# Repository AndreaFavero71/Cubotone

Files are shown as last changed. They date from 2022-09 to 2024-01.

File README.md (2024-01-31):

# CUBOTone

This repo contains the files to build CUBOTone, my first Rubik’s cube solver robot.<br />
CUBOTone uses servos and stepper motor resulting in a faster solving time than the newer CUBOTino series.

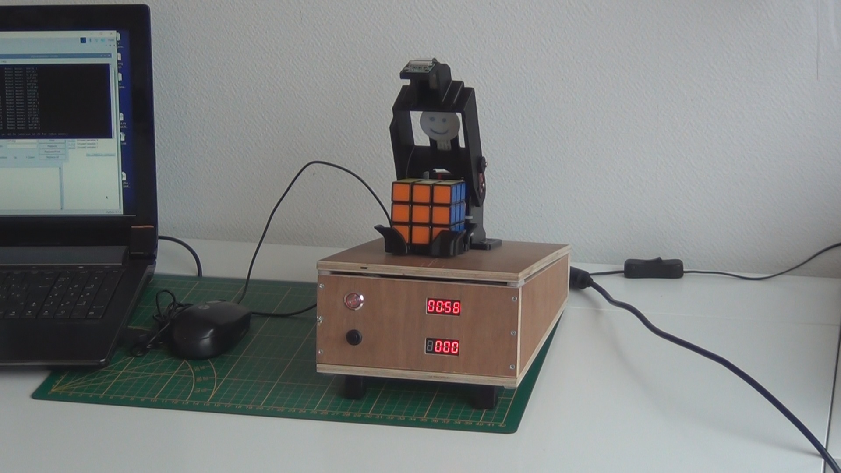
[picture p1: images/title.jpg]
title image


Further robot info at: https://www.instructables.com/Rubik-Cube-Solver-Robot-With-Raspberry-Pi-and-Pica/

An impression of the robot: https://www.youtube.com/watch?v=oYRXe4NyJqs

This git repo simplifies the download of the individual files and automates as much a possible the deployment to the Raspberry Pi

# How to use it:
1. Flash your SD card according to the procedure in the [document here](doc/How_to_make_CUBOTone_robot_20240131.pdf) , Chapter 8
2. Put the sd card in the pi and power it. You can monitor the boot process if you connect an hdmi monitor to it but it is not essential. 
3. Try to connect to the Raspberry Pi via SSH. On Windows you can use Putty. On linux and mac you can type directly:
```
ssh pi@cubotone.local
```
4. If you can’t reach the pi like this, you will have to scan your network to find the IP to use
5. After you are connected via ssh, type the following commands in the shell:
```
git clone https://github.com/AndreaFavero71/cubotone.git
cd cubotone/src
sudo ./install/setup.sh
```
6. Make sure the script runs without error until the end. It should ask you to reboot. Type ‘y’ and hit enter. You should get the proper environment after reboot at that point
7. If there is any error during the script execution try to fix it and rerun the script again

# Executing manually
From a shell, you can run the main python script like this:
```
cd ~/cubotone/src
source .virtualenvs/bin/activate
python Cubotone.py
```
of course, you can replace `Cubotone.py` by any other python scripts as mentioned in the documentation.

# Enabling autostart
When everything is tuned and you want to autostart the software automatically on reboot, just type :
```
    sudo crontab -e
```
select the nano editor ‘1’ then go to the last line of the window and remove the first ‘#’ character of the line . This uncomment the startup script that launches cubotino on startup. You can reboot after to test it.

# VNC connection
You can always connect with ssh. If you prefere VNC you can download the RealVNC client (this is the one I use). You just have that start it like this:
```
vncviewer cubotone.local
```
It will ask for the credential. Use ‘pi’ and the same password you use for ssh. You should have a desktop version in this way

Check out the "How_to_make ...  .pdf" document (at /doc folder) for further info

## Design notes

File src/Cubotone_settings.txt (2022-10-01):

{
"camera_width_res": "800",
"camera_hight_res": "544",
"zoom_x":0.0,
"zoom_y":0.0,
"zoom_w":1,
"zoom_h":1,
"kl": "0.95",
"scale_perc": "65",
"square_ratio": "2",
"rhombus_ratio": "0",
"delta_area_limit": "0.7",
"sv_max_moves": "20",
"sv_max_time": "2",
"collage_w": "1024",
"marg_coef": "0.1",
"cam_led_bright": "300",
"detect_timeout": "40",
"show_time": "7",
"gap_w": "60",
"gap_h": "100"
}

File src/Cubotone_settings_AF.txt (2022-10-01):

{
"camera_width_res": "800",
"camera_hight_res": "544",
"zoom_x":0.0,
"zoom_y":0.0,
"zoom_w":0.75,
"zoom_h":0.82,
"kl": "0.95",
"scale_perc": "65",
"square_ratio": "2",
"rhombus_ratio": "0",
"delta_area_limit": "0.7",
"sv_max_moves": "20",
"sv_max_time": "2",
"collage_w": "1024",
"marg_coef": "0.1",
"cam_led_bright": "300",
"detect_timeout": "40",
"show_time": "7",
"gap_w": "60",
"gap_h": "100"
}

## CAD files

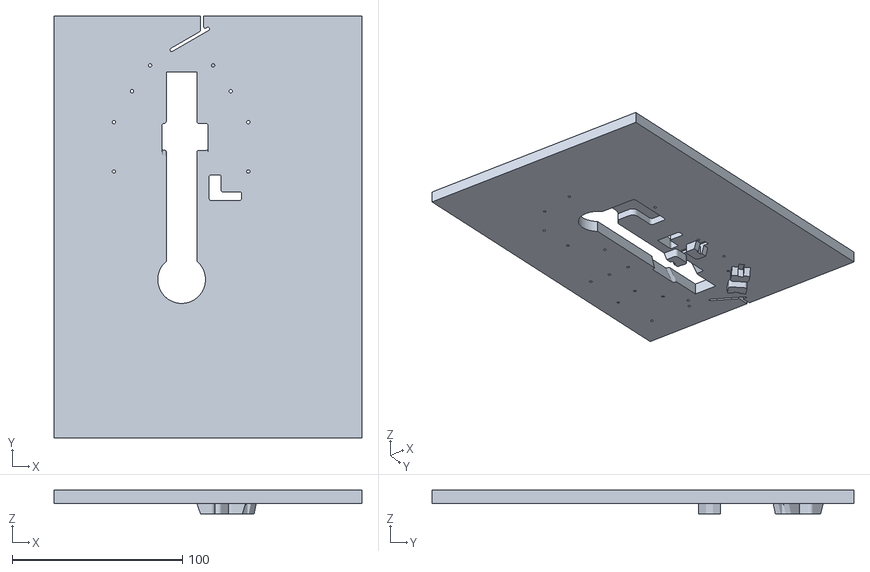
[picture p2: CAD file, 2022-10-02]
stl/Panel_top.stl
181.0 x 248.0 x 14.0

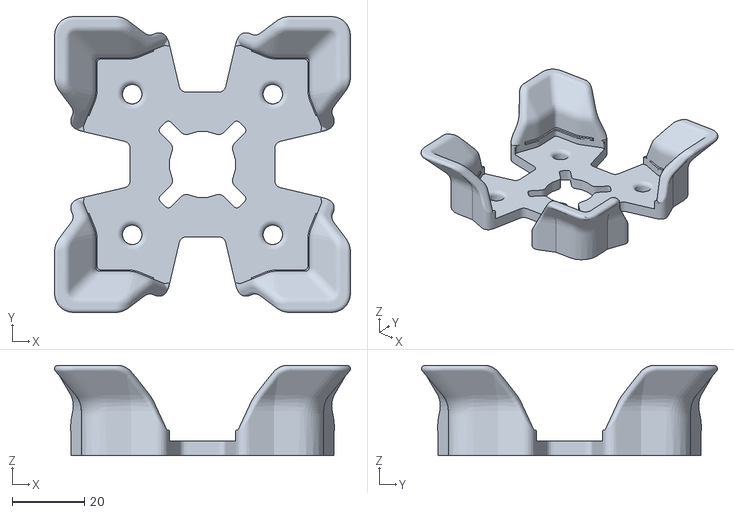
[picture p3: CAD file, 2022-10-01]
stl/Cube_holder_upper_part.stl
81.9 x 81.9 x 25.0

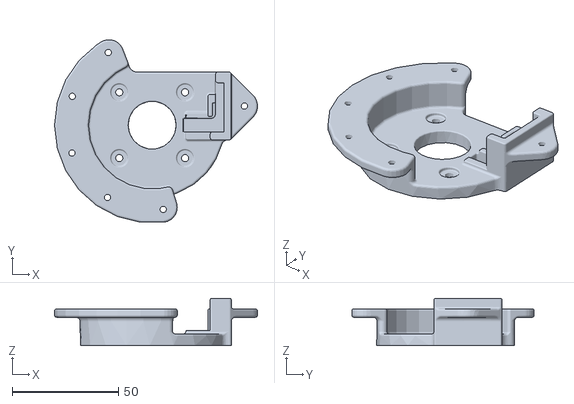
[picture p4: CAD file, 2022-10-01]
stl/Motor_support.stl
95.6 x 85.9 x 22.1

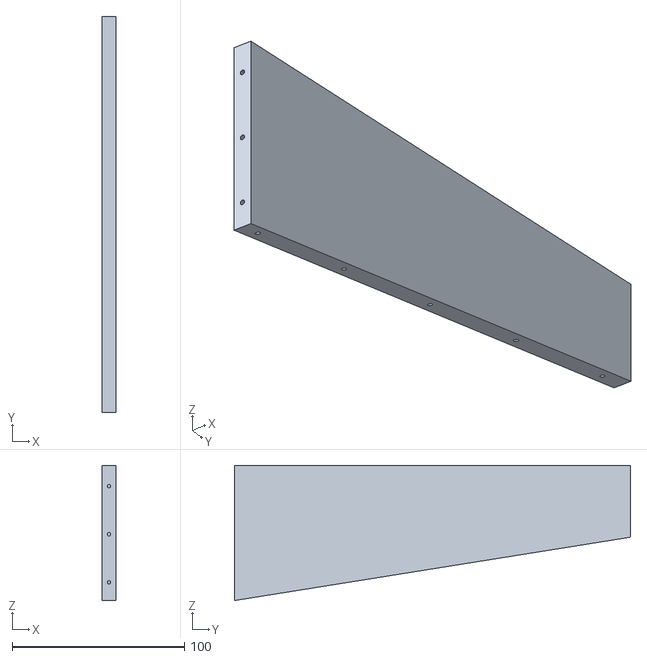
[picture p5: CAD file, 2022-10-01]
stl/Panel_left.stl
8.00 x 230.0 x 78.5

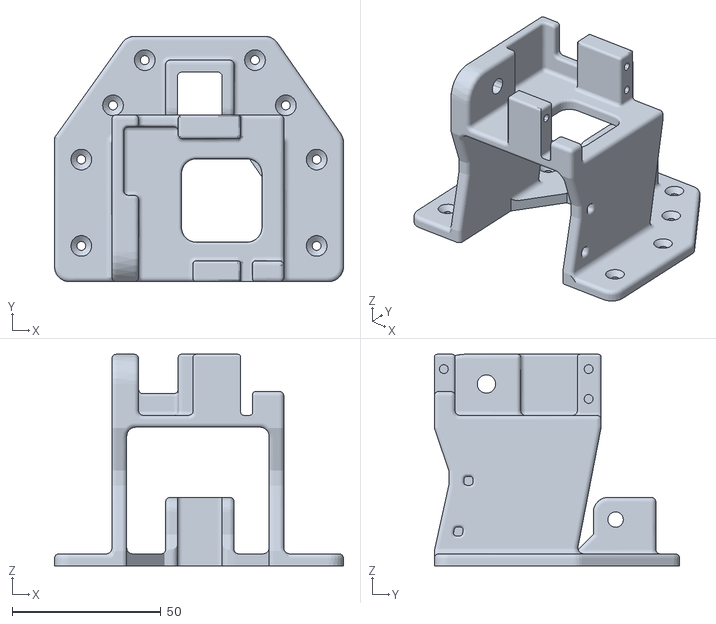
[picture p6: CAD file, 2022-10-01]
stl/Hinge_upperCover_Lifter.stl
97.0 x 82.4 x 71.0

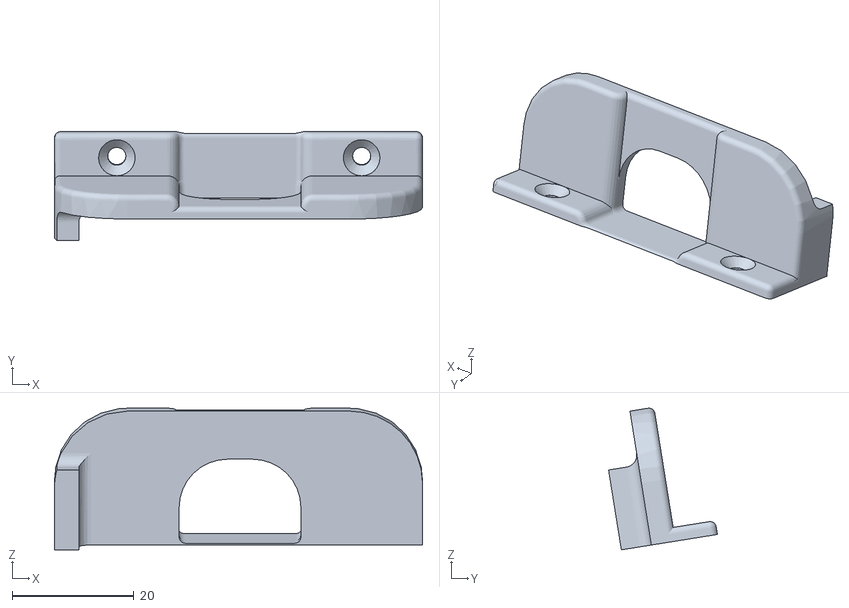
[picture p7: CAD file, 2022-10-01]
stl/Rpi_holder_back.stl
60.5 x 17.9 x 23.3

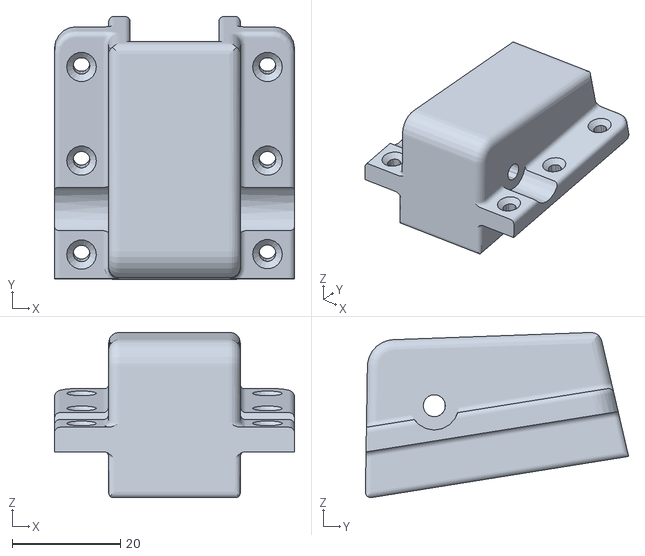
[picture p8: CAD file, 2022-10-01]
stl/Foot_hinge.stl
44.4 x 48.7 x 30.5

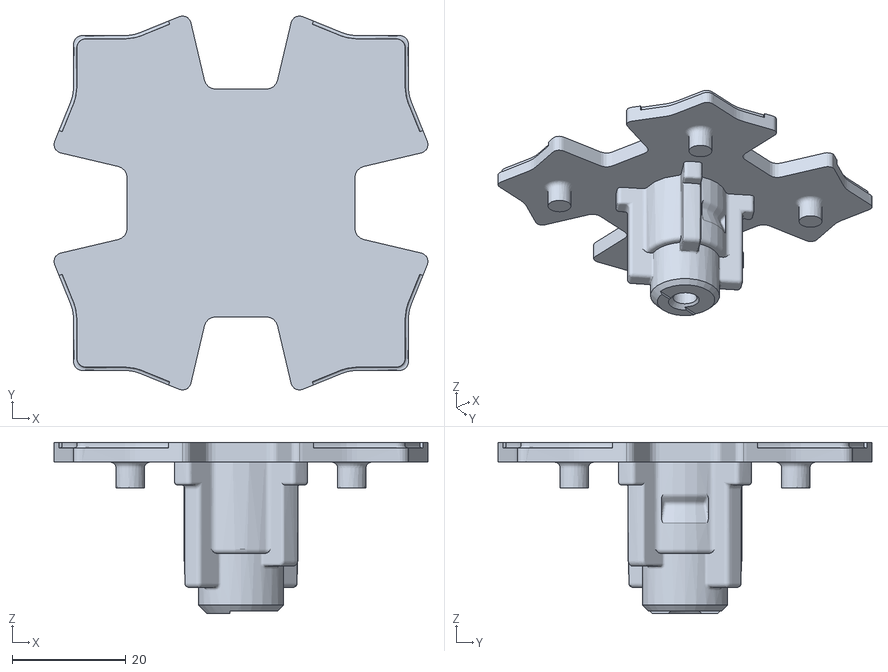
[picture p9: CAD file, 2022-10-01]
stl/Cube_holder_lower_part.stl
65.7 x 65.7 x 30.1

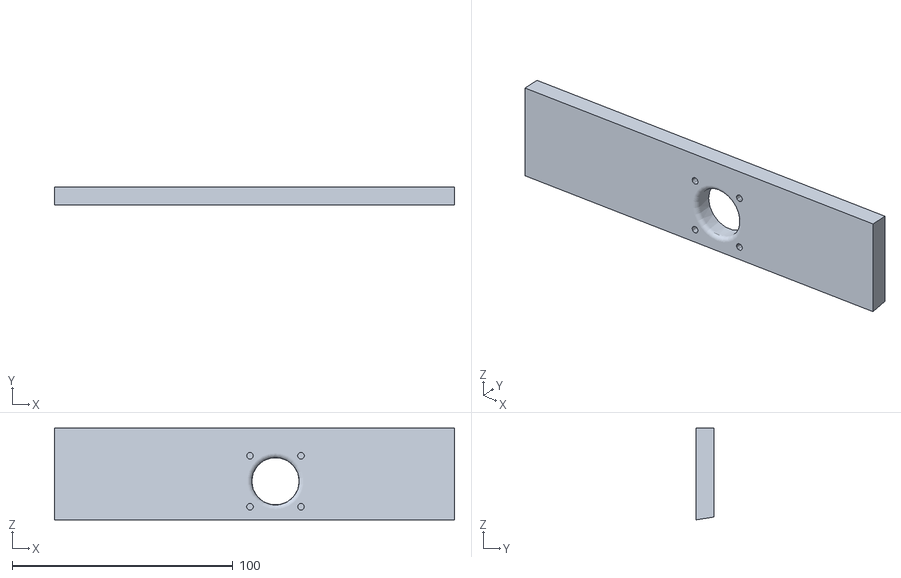
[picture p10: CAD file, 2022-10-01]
stl/Panel_back.stl
181.0 x 8.00 x 41.5

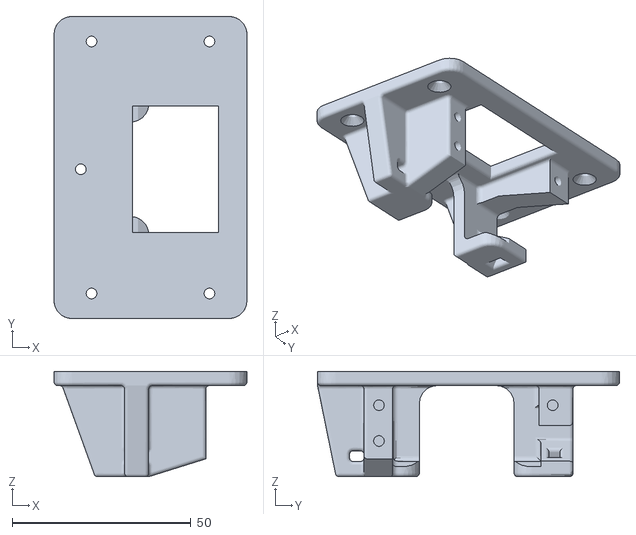
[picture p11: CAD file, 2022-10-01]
stl/Lifter_servo_holder.stl
54.0 x 84.5 x 29.5

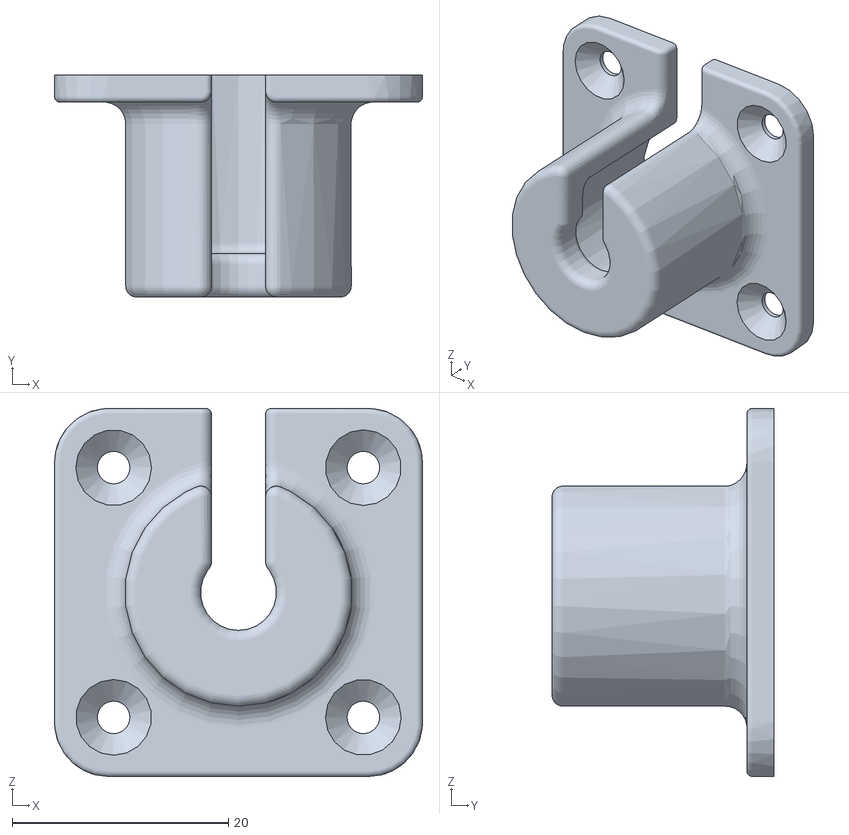
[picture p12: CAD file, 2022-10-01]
stl/Power_connector_inner_part.stl
34.0 x 20.5 x 34.0

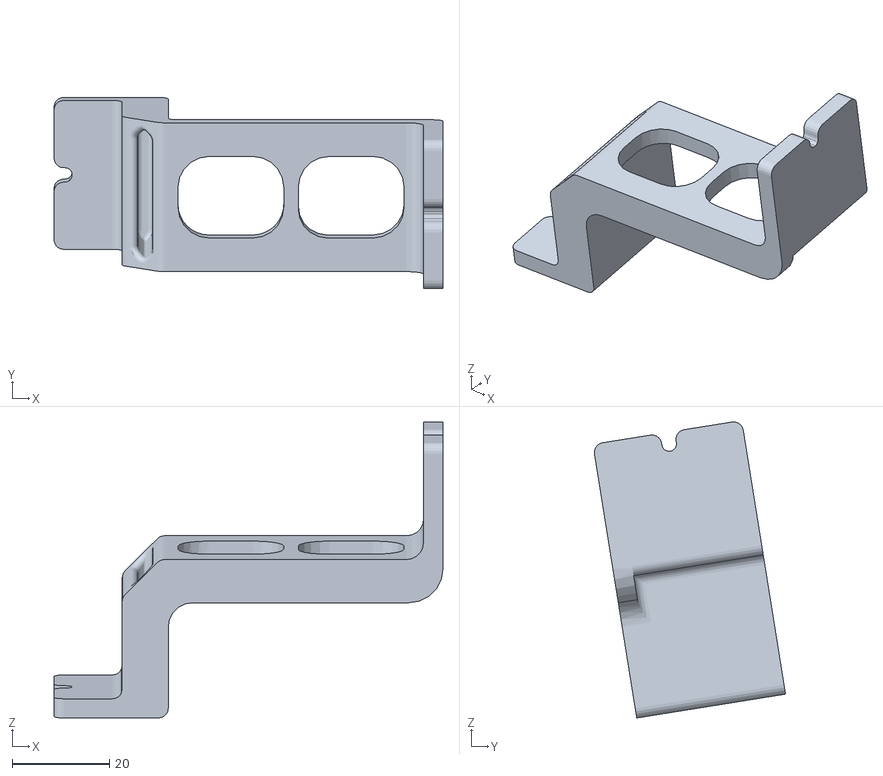
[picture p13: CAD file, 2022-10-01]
stl/Rpi_holder_front.stl
80.0 x 39.3 x 60.9

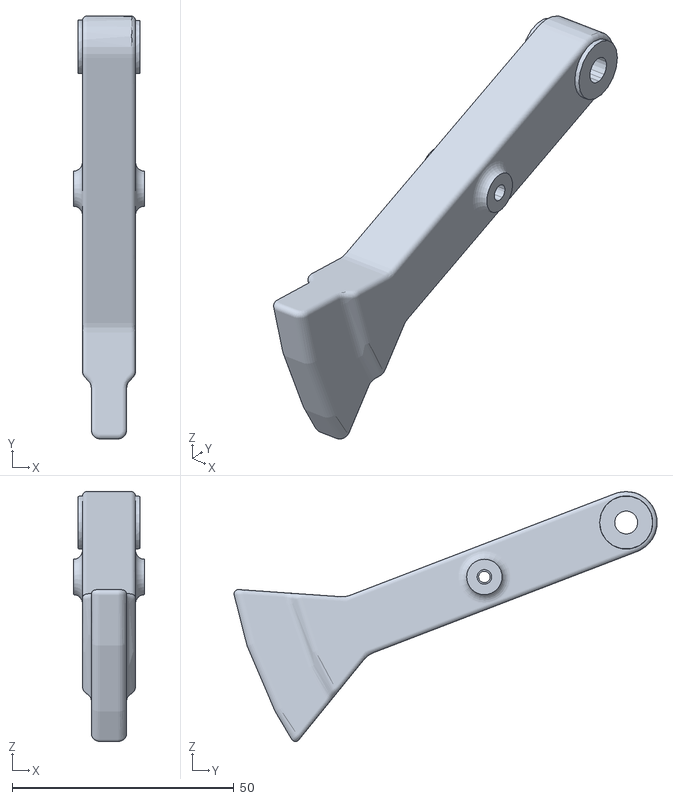
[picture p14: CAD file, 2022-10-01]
stl/Lifter.stl
16.0 x 95.5 x 56.4

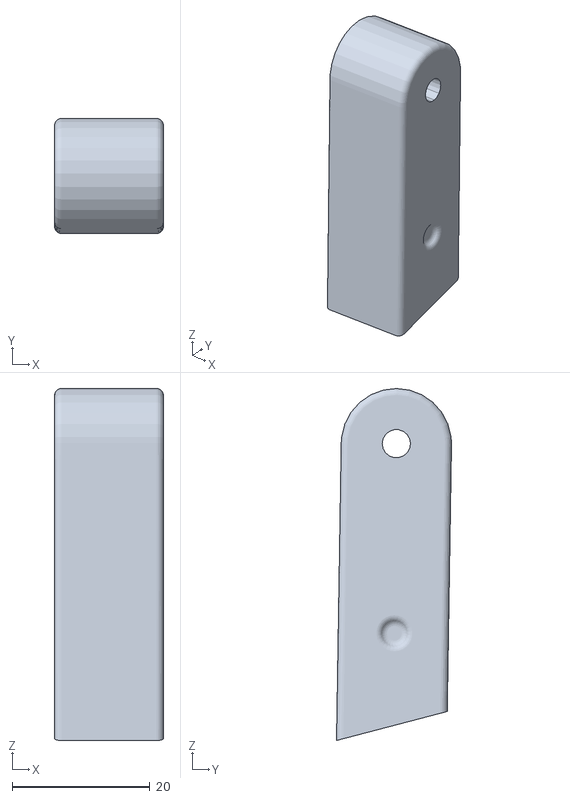
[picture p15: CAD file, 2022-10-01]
stl/Foot.stl
15.8 x 16.7 x 51.0

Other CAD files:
stl/PiCamera_holder.stl
stl/Power_connector_outer_part.stl
stl/Lever_link.stl
stl/Panel_bottom.stl
stl/Motor_sync_disk.stl
stl/Panel_front.stl
stl/Panel_right.stl

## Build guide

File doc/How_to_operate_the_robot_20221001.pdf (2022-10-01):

How to operate the robot: | 01 October 2022

Robot instructions (How_to_operate_the_robot_20221001.docx or .pdf):

SHUTDOWN: Closes the Raspberry Pi OS, wait 15 seconds before to unplug the robot.
BOOT: After a shutdown, a short press starts the boot (takes 30secs to complete); Boot starts automatically after the robot is plugged.
START: Only when Display2 shows Press.
STOP: Stops the robot, at any moment, when it is “moving”; If the button is released within 5 seconds the python script is reloaded and the robot gets ready again for a new cycle.
RESET: Ends the python script. Raspberry Pi OS remains up (use SHUTDOWN before unplug).

The robot has 2 main working modes:
A) Without any screen connected; This is the default mode, that starts once the robot is energized.
B) With a screen connected, by wiring or via SSH.

To quit mode A) or B), press STOP for 5 seconds. Displays segments go full ON and OFF shortly after.

To start mode B):
- Quit mode A)
- Connect to the raspberry pi (i.e. with VNC viewer, via SSH)
- Activate the virtual environment (source /home/pi/.virtualenvs/bin/activate)
- From root (/home/pi) enter the cube folder (cd cubotone/src)
- Run the python script (python Cubotone.py)
- SHUTDOWN (led goes OFF)
- BOOT (led goes ON in 30 secs)
- LOADING STATUS
- TIMER
- START
- STOP (0.5s < press < 5 sec)
- RESET (>5 sec press)
- INFO
- COUNTDOWN MOVES

## Display 1

## Display 2

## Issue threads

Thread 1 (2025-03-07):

Installation Issues: opencv-contrib-python==4.1.0.25 Not Found & CMake Build Fails with pytoml.core.TomlError

chiptrap, 2025-03-07:
Hello,

I'm experiencing two separate issues while attempting to install our OpenCV dependency for the Cubotone project on my Raspberry Pi 4. Below are the two error messages I’m encountering:

Error 1: Version Not Found

When I try to install:

`pip install opencv-contrib-python==4.1.0.25`
I receive the following error:

```
Could not find a version that satisfies the requirement opencv-contrib-python==4.1.0.25 (from versions: 3.4.11.45, 3.4.13.47, 3.4.14.51, 3.4.15.55, 3.4.16.59, 3.4.17.61, 3.4.17.63, 3.4.18.65, 4.4.0.46, 4.5.1.48, 4.5.2.52, 4.5.3.56, 4.5.4.58, 4.5.4.60, 4.5.5.62, 4.5.5.64, 4.6.0.66, 4.7.0.68, 4.7.0.72, 4.8.0.74, 4.8.0.76, 4.8.1.78, 4.9.0.80, 4.10.0.82, 4.10.0.84, 4.11.0.86)
No matching distribution found for opencv-contrib-python==4.1.0.25
It appears that version 4.1.0.25 is no longer available on PyPI (or piwheels). I’ll need to update our dependency to one of the available versions.
```

Error 2: When attempting to adjust the setup.sh to use a closer version like 4.4.0.46 I receive the output

`Command "/home/pi/cubotone/src/.virtualenvs/bin/python3 -m pip install --ignore-installed --no-user --prefix /tmp/pip-build-env-_271njy9 --no-warn-script-location --no-binary :none: --only-binary :none: -i https://pypi.org/simple --extra-index-url https://www.piwheels.org/simple -- setuptools wheel scikit-build cmake pip "numpy==1.13.3; python_version=='3.6' and platform_machine != 'aarch64' and platform_machine != 'arm64'" "numpy==1.14.5; python_version=='3.7' and platform_machine != 'aarch64' and platform_machine != 'arm64'" "numpy==1.17.3; python_version=='3.8' and platform_machine != 'aarch64' and platform_machine != 'arm64'" "numpy==1.19.3; python_version<='3.9' and sys_platform == 'linux' and platform_machine == 'aarch64'" "numpy==1.21.0; python_version<='3.9' and sys_platform == 'darwin' and platform_machine == 'arm64'" "numpy==1.19.3; python_version=='3.9' and platform_machine != 'aarch64' and platform_machine != 'arm64'" "numpy==1.21.2; python_version>='3.10'"" failed with error code 2 in None`

Environment Details:

Hardware: Raspberry Pi 4
OS: Raspbian GNU/Linux 10 (buster)
Python: 3.7 (running in a virtual environment at /home/pi/cubotone/src/.virtualenvs)
pip: 18.1
scikit-build: >= 0.14.0
Steps I’ve Tried:

Upgrading pip, setuptools, and scikit-build.
Using the flags --no-binary :none: and --only-binary :none: to force a source build (which triggers a TOML parsing error).
Specifying opencv-contrib-python version 4.1.0.25 (which is unavailable) in our requirements.
Examining the error output from cmake’s build process, which indicates that line 69 of pyproject.toml is missing an expected '='.
Questions:

Regarding the Version Error:

Should we update our dependency to one of the available versions (e.g., 4.5.1.48 or the latest 4.11.0.86) for our Raspberry Pi 4 environment?

AndreaFavero71, 2025-03-09:
Hi, I confirm the issue you raised.
In the `cubotone/src/install/setup.sh` please replace `pip install opencv-contrib-python==4.1.0.25` with `pip install opencv-python==4.1.0.25`.
I have just made a quick test and it seems working fine (the _contrib_ part of opencv is not used by this robot).
Please feedback

chiptrap, 2025-03-10:
Hello, it seems that the issue might lie in the use of an RPI4. I'm still receiving the same errors even with the relevant changes. It seems there is not an aarch64 compatible download of the library for that version. When I adjust the code to read `pip install opencv-python==4.1.0.25` I receive the same build dependency error. I don't have access to a pizero to test.
The only working version of opencv-python that I could manage to install was 4.11.0.86 and 4.5.1.48, which are both aarm64 compatible. I'm relatively new so I could be confused but it seems that the currently supplied version of opencv-python is only compatible with the pi zero

chiptrap, 2025-03-10:
I did some more digging and it seems it was because I was using a depreciated version of pip. This might be relevant to update in the setup.sh because it seems to be an obscure error that effects pip versions earlier than 19.3
[Link to PyPi opencv docs](https://pypi.org/project/opencv-python/#frequently-asked-questions)

AndreaFavero71, 2025-03-10:
You're right, that was the problem.
I've added the pip ugrade in setup.sh

Closed 2025-03-10.

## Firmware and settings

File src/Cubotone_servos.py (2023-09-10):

#!/usr/bin/python
# coding: utf-8

"""
#############################################################################################################
# Andrea Favero   rev 10 September 2023
#
# This script relates to CUBOTone, my first simple Rubik's cube solver robot
# This specific script controls two servos, one stepper motor, and led module
# 
# Possible moves with this robot
# 1) Spins the complete cube ("S") laying on the bottom face: 1 means CW 90deg turns, while 3 means 90CCW turn
# 2) Flips the complete cube ("F") by "moving" the Front face to Bottom face: Only positive values are possible
# 3) Rotates the bottom layer ("R") while costraining the 2nd and 3rd layer.
# 4) The order of S, F has to be strictly followed
# 5) Example 'F1R1S3' means: 1x cube Flip, 1x (90deg) CW rotation of the 1st (Down) layer, 1x (90deg) CCW cube Spin
#
# For Rotations, the stpper motor makes a little extra rotation than target, before coming back to target; This
# is needed to recover the gaps between cube_hoder - cube - top_cover, and still getting a decent cube layers alignment.
#
#
#############################################################################################################
"""

import Adafruit_PCA9685              # Import the PCA9685 module, used to control two servos via the I2C
import RPi.GPIO as GPIO              # import RPi GPIO
import time
from time import sleep

# GPIO pins assigments
stepper_enable = 22                  # GPIO pin used to ebale/disable the stepper motor driver
stepper_dir = 17                     # GPIO pin used to control the stepper motor direction 
stepper_step = 27                    # GPIO pin used to generate the stepper motor steps
stepper_ms2 = 5                      # GPIO pin used to change the stepper motor micro-step
light_gate = 4                       # GPIO pin used to for the light_gate input signal
srv_cover = 15                       # GPIO pin used to control the top cover servo 
srv_flipper = 14                     # GPIO pin used to control the flipper servo
led1=13                              # GPIO pin used to control the led1 on top cover 
led2=12                              # GPIO pin used to control the led2 on top cover 

# overall GPIO settings
GPIO.setmode(GPIO.BCM)               # setting GPIO pins as "Broadcom SOC channel" number, these are the numbers after "GPIO"
GPIO.setwarnings(False)              # setting GPIO to don't return allarms

# stepper motor GPIO pins settings
GPIO.setup(stepper_enable,GPIO.OUT)  # GPIO pin used to ebale/disable the stepper motor driver is set as output
GPIO.setup(stepper_dir,GPIO.OUT)     # GPIO pin used to control the stepper motor direction is set as output
GPIO.setup(stepper_step,GPIO.OUT)    # GPIO pin used to generate the stepper motor steps is set as output
GPIO.setup(stepper_ms2,GPIO.OUT)     # GPIO pin used to change the stepper motor micro-step (MS2) is set as output

# light_gate GPIO pin setting
GPIO.setup(4,GPIO.IN)                # motor position sensor


def init_PCA9685():
    """ Function to initialize the PCA9685 board.
        Adafruit 16-Channel 12-bit PWM/Servo Driver - I2C interface - PCA9685."""
    
    global pwm

    try:
        pwm = Adafruit_PCA9685.PCA9685()     # Initialise the PCA9685 using the default address (0x40).
        pwm.set_pwm_freq(60)                 # sets the frequency to 60hz, good for servos.
        pwm.set_pwm(srv_cover, 0, 0)         # servo is forced off
        pwm.set_pwm(srv_flipper, 0, 0)       # servo is forced off
        pwm.set_pwm(led1, 0, 0)              # led1 is forced off, 60Hz is ok to set the output off for the led
        pwm.set_pwm(led2, 0, 0)              # led2 is forced off, 60Hz is ok to set the output off for the led
    except:
        print(f"\n\n#############################################################################")
        print("WARNING: failed to load Adafruit_PCA9685 module")
        print("This happens if the module is not found at the I2C, or library not installed.")
        print(f"#############################################################################\n")
        raise




def init_servo(servos_init, debug, motor_hw = True):
    """ Function to initialize the robot (servos and motor position) and some global variables, do be called once, at the start.
    Parameters are imported from a json file, to make easier to list/document/change the variables
    that are expected to vary on each robot.
    These servo_settings are under a function, instead of root, to don't be executed when this script is used from CLI
    with arguments; In this other case the aim is to help setting the servo to their mid position."""
    
    global cover_close, cover_open, cover_read, flipper_low, flipper_high
    global time_cover_closing, time_cover_opening, time_cover_reading
    global time_flipper_low, time_flipper_high, time_consec_flip
    global ramp, spin_fast_ramp, spin_slow_ramp, time_on_spin_fast, time_on_spin_slow
    global align_repeats, time_on_align_fast, time_on_align_precise, timeout
    global stp_rev, extra_steps_s, extra_steps_m, extra_steps_align, align_blind_steps
    global led_brightness, motor_reversed, motors    
    
    if not servos_init:                                               # case the inititialization status of the servos is false

        if motor_hw:                                                  # case the motor_hd variable is True
            motors = True                                             # global variable motors is set True
            init_PCA9685()                                            # PCA9685 initialization function is called
        else:                                                         # case the motor_hd variable is False
            motors = False                                            # global variable motors set False
        
        # convenient choice for Andrea Favero, to upload the settings fitting my robot, via mac address check                
        from getmac import get_mac_address                            # library to get the device MAC ddress
        import os.path, pathlib, json                                 # libraries needed for the json, and parameter import
        
        folder = pathlib.Path().resolve()                             # active folder (should be home/pi/cube)  
        eth_mac = get_mac_address()                                   # mac address is retrieved
        if eth_mac == 'e4:5f:01:0a:31:ce':                            # case the script is running on AF (Andrea Favero) robot
            fname = os.path.join(folder,'Cubotone_servos_settings_AF.txt')  # AF robot settings (do not use these at the start) 
        else:                                                         # case the script is not running on AF (Andrea Favero) robot
            fname = os.path.join(folder,'Cubotone_servos_settings.txt')  # folder and file name for the settings, to be tuned               
        
        if os.path.exists(fname):                                           # case the servo_settings file exists
            with open(fname, "r") as f:                                     # servo_settings file is opened in reading mode
                servo_settings = json.load(f)                               # json file is parsed to a local dict variable
            
            if debug:                                                       # case the variable debug is set True
                print('\nimporting servos settings from the text file:', fname)    # feedback is printed to the terminal
                print('imported servos settings:')                                 # feedback is printed to the terminal
                for parameter, setting in servo_settings.items():           # iteration over the settings dict
                    print(parameter,': ', setting)                          # feedback is printed to the terminal
                print()
                
            backup_fname = os.path.join(folder,'Cubotone_servos_settings_backup.txt')  # folder and file name for the settings backup
            with open(backup_fname, 'w') as f:                                    # servo_settings_backup file is opened in writing mode
                f.write(json.dumps(servo_settings, indent=0))                     # content of the setting file is saved in another file, as backup
                if debug:                                                         # case the variable debug is set True
                    print('\nsaving a backup text file of the settings:', fname)  # feedback is printed to the terminal
                    print()
            
            try:
                cover_close = int(servo_settings['cover_close'])                  # Top_cover close position
                cover_open = int(servo_settings['cover_open'])                    # Top_cover open position
                cover_read = int(servo_settings['cover_read'])                    # Top_cover camera read position
                flipper_low = int(servo_settings['flipper_low'])                  # Top_cover flip low position
                flipper_high = int(servo_settings['flipper_high'])                # Top_cover flip high position
                time_cover_closing = float(servo_settings['time_cover_closing'])  # time for Top_cover to reach the close position
                time_cover_opening = float(servo_settings['time_cover_opening'])  # time for Top_cover from close to flip position
                time_cover_reading = float(servo_settings['time_cover_reading'])  # time for Top_cover to reach the read position
                time_flipper_low = float(servo_settings['time_flipper_low'])      # time for Flipper to reach the low position
                time_flipper_high = float(servo_settings['time_flipper_high'])    # time for Flipper to reach the high position
                time_consec_flip = float(servo_settings['time_consec_flip'])      # time for consecutive flipping, when a flip is followed by others
                
                ramp = float(servo_settings['ramp'])                              # time variation for the stepper motor ramp
                spin_fast_ramp = float(servo_settings['spin_fast_ramp'])          # time variation for the stepper motor ramp, when spinning fast
                spin_slow_ramp = float(servo_settings['spin_slow_ramp'])          # time variation for the stepper motor ramp, when spinning slow
                time_on_spin_fast = float(servo_settings['time_on_spin_fast'])    # time ON stepper for spinning fast
                time_on_spin_slow = float(servo_settings['time_on_spin_slow'])    # time ON stepper for spinning slow
                time_on_align_fast = float(servo_settings['time_on_align_fast'])  # time ON stepper for alignment fast part
                time_on_align_precise = float(servo_settings['time_on_align_precise'])  # time ON stepper for alignment precise part
                
                stp_rev = int(servo_settings['stp_rev'])                          # number of motor steps per revolution, considering the microstep setting
                extra_steps_s = int(servo_settings['extra_steps_s'])              # number of motor additional steps when rotating 90 deg (s=single rot)
                extra_steps_m = int(servo_settings['extra_steps_m'])              # number of motor additional steps when rotating more than 90 deg (m=multi rot)
                extra_steps_align = int(servo_settings['extra_steps_align'])      # number of motor additional steps when aligning the motor
                align_blind_steps = int(servo_settings['align_blind_steps'])      # number of initial motor steps, at precise alignment, to 're-enter' the sync. disk slots
                align_repeats = int(servo_settings['align_repeats'])              # max number of motor alignment iterations, when not ending successfully
                timeout = float(servo_settings['timeout'])                        # timeout in secs for motor alignment
                motor_reversed = int(servo_settings['motor_reversed'])            # reverse the motor direction behavior (0=default, 1=reversed)
                
                if motor_reversed <= 0:                                           # case the motor_reversed argument is <= zero
                    motor_reversed = 0                                            # motor_reversed variable is set to zero
                elif motor_reversed >= 1:                                         # case the motor_reversed argument is >= one
                    motor_reversed = 1                                            # motor_reversed variable is set to one

                servo_start_positions(debug)                                      # servos are positioned to the start position
                led_test(debug)                                                   # top_cover Leds are shortly energized as feedback
                led_off()                                                         # top_cover Led are set off
                servos_init = True                                                # servos_init_status variable is set True
                
                return servos_init                                                # return servos_init_status variable
            
            
            except:   # exception will be raised if json keys differs, or parameters cannot be converted to float
                print('\nerror on converting to float the imported parameters')   # feedback is printed to the terminal                                  
                servos_init = False                                               # servos_init_status variable is set False
                return servos_init                                                # return servos_init_status variable
        
        else:                                                                     # case the servo_settings file does not exists, or name differs
            print('\ncould not find Cubotino_T_servo_settings.txt')                 # feedback is printed to the terminal                                  
            servos_init = False                                                   # servos_init_status variable is set False
            return servos_init                                                    # return servos_init_status variable





def extra_rotation_adj(debug, cube_size_adj):
    """modifies the extra rotations (SPIN and ROTATE) based on the cube size difference from the default setting.
       Cube size difference is expressed in tent of millimeters"""
    
    global extra_steps_s, extra_steps_m
    
    if debug:                                  # case the variable debug is set True
        print("original extra_steps_s", extra_steps_s)  # feedback is printed to Terminal
        print("original extra_steps_m", extra_steps_m)  # feedback is printed to Terminal
        
    extra_steps_s = int(extra_steps_s - cube_size_adj*extra_steps_s/20)  # extra_steps_s is adjusted
    extra_steps_m = int(extra_steps_m - cube_size_adj*extra_steps_m/20)  # extra_steps_m is adjusted
    
    if debug:                                  # case the variable debug is set True
        print("adjusted extra_steps_s", extra_steps_s)  # feedback is printed to Terminal
        print("adjusted extra_steps_m", extra_steps_m)  # feedback is printed to Terminal




def servo_freq(debug):
    """sets the PCA9685 output frequency for the servo. Servo require tipically 60Hz."""
    
    if not motors:
        return
    
    pwm.set_pwm_freq(60)                        # sets the frequency to 60Hz
    time.sleep(0.05)                            # little time sleep to let the parameter change to get processed by the PCA 9685 board
#     if debug:                                   # case the variable debug is set True
#         print('frequency to 60Hz to PCA 9685 board, for servo control') # feedback is printed to the terminal





def led_freq(debug):
    """sets the PCA9685 output frequency for the leds. PWM Leds at 60Hz is bad for the camera, and at least 1KHz needed."""
    
    if not motors:
        return
    
    servo_off(debug=False)                      # set the servo to off, to prevent unexpected reaction at the frequency change
    pwm.set_pwm_freq(1000)                      # sets the frequency to 1000Hz
    time.sleep(0.05)                            # little time sleep to let the parameter change to get processed by the PCA 9685 board
#     if debug:                                   # case the variable debug is set True
#         print('frequency set to 1000Hz to PCA 9685 board, for led control') # feedback is printed to the terminal





def servo_start_positions(debug,wait_time=True):
    """initial position for the top cover and cube flipper; The parameter defines the sleep time before returning"""
    
    if not motors:
        return

    servo_freq(debug)
    read_cover()                                # initial position for the cover is fully high, to prevent interference with base rotation while zeroing it                             
    if wait_time:                               # case wait_time in ar is left as per default
        time.sleep(0.4)                         # extra time to ensure the parts are moved and the innertia has dropped
    cube_flipper_low(time_flipper_low)          # initial position for the flipper is fully high, to prevent interference with base rotation while zeroing it
    if wait_time:                               # case wait_time in ar is left as per default
        time.sleep(0.4)                         # extra time to ensure the parts are moved and the innertia has dropped
    if debug:                                   # case the variable debug is set True
        print('servos to the start position')   # feedback is printed to the terminal




def servo_off(debug):
    """disable the servo."""
    
    if not motors:
        return
    
    time.sleep(0.2)                        # some little wait time to ensure servos have completed the eventual movement, prior removing the PWM
    pwm.set_pwm(srv_cover, 0, 0)           # servo is forced off, in case the target wasn't reached in time (blocked movement)
    pwm.set_pwm(srv_flipper, 0, 0)         # servo is forced off, in case the target wasn't reached in time (blocked movement)
    if debug:                              # case the variable debug is set True
        print('servos are disabled')       # feedback is printed to the terminal




def led_cover(value=200):
    """ Sets the top_cover led ON, with brightness in arg. Value ranges from 0 to 4095, yet it will be limited to 2000"""

    if not motors:
        return
    
    if value >= 2000:                     # case arg is bigger than, or equal to 1200
        pwm.set_pwm(led1, 0, 2000)        # led1 is energized at 2000 (ca 50% of max intensity)
        pwm.set_pwm(led2, 0, 2000)        # led2 is energized at 2000 (ca 50% of max intensity)
    else:                                 # case arg is smaller than 1200
        pwm.set_pwm(led1, 0, value)       # led1 is energized at value
        pwm.set_pwm(led2, 0, value)       # led2 is energized at value




def led_off():
    """disable the led."""
    
    if not motors:
        return
    
    pwm.set_pwm(led1, 0, 0)               # led1 is forced off
    pwm.set_pwm(led2, 0, 0)               # led2 is forced off




def led_test(debug):
    """ Fade the led On and Off at the init, to show the led worwing."""
    
    if not motors:
        return
    
    led_freq(debug)
    for i in range(0,800,50):            # iterates from 0 to 700 in steps of 100
        pwm.set_pwm(led1, 0, i)           # led1 is energized at iterator value
        pwm.set_pwm(led2, 0, i)           # led2 is energized at iterator value
        time.sleep(0.01)                   # very short time sleep
    
    for i in range(700,-50,-50):        # iterates from 700 to 0 in steps of -100 
        pwm.set_pwm(led1, 0, i)           # led1 is energized at iterator value
        pwm.set_pwm(led2, 0, i)           # led2 is energized at iterator value
        time.sleep(0.01)                  # very short time sleep
    servo_freq(debug)




def read_cover():
    """Top cover position fully opened; The parameter defines the sleep time before returning""" 

    if not motors:
        return
    
    pwm.set_pwm(srv_cover, 0, cover_read)   # pwm to the servo to reach the target position
    sleep(time_cover_reading)  # (AF 0.18)  # time necessary to servo to reach the target




def open_cover(fast_speed=False):
    """Top cover position fully opened; The parameter defines the sleep time before returning""" 
    
    if not motors:
        return

    if fast_speed==True:
        pwm.set_pwm(srv_cover, 0, cover_open)    # pwm to the servo to reach the target position, without sleep time afterward
        sleep(time_cover_opening-0.05)           # (AF 0.1)   # time necessary to servo to get the top_cover out from the cube
    
    else:
        pwm.set_pwm(srv_cover, 0, cover_open)    # pwm to the servo to reach the target position, followed by a sleep time
        sleep(time_cover_opening)  # (AF 0.15)   # time necessary to servo to reach the target




def close_cover():
    """Top cover position fully closed; The parameter defines the sleep time before returning""" 
    
    if not motors:
        return
    
    pwm.set_pwm(srv_cover, 0, cover_close)       # pwm to the servo to reach the target position
    sleep(time_cover_closing)  # (AF 0.22)       # time necessary to servo to reach the target
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

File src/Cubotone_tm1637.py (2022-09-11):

#!/usr/bin/env python
# -*- coding: utf-8 -*-


# from https://github.com/Bogdanel/Raspberry-Pi-Python-3-TM1637-Clock
# resume table with possible letters 

"""
Display	Bin	Hex	Dec	HexDigit Index
0	0b00111111	0x3F	63	0
1	0b00000110	0x06	6	1
2	0b01011011	0x5B	91	2
3	0b01001111	0x4F	79	3
4	0b01100110	0x66	102	4
5	0b01101101	0x6D	109	5
6	0b01111101	0x7D	125	6
7	0b00000111	0x07	7	7
8	0b01111111	0x7F	127	8
9	0b01101111	0x6F	111	9
A	0b01110111	0x77	119	10
b	0b01111100	0x7C	124	11
C	0b00111001	0x39	57	12
d	0b01011110	0x5E	94	13
E	0b01111001	0x79	121	14
F	0b01110001	0x71	113	15
G	0b00111101	0x3D	61	16
H	0b01110110	0x76	118	17
I	0b00000110	0x06	6	18
J	0b00011110	0x1E	30	19
K	0b01110110	0x76	118	20
L	0b00111000	0x38	56	21
M	0b01010101	0x55	85	22
n	0b01010100	0x54	84	23
O	0b00111111	0x3F	63	24
P	0b01110011	0x73	115	25
q	0b01100111	0x67	103	26
r	0b01010000	0x50	80	27
S	0b01101101	0x6D	109	28
t	0b01111000	0x78	120	29
U	0b00111110	0x3E	62	30
v	0b00011100	0x1C	28	31
W	0b00101010	0x2A	42	32
X	0b01110110	0x76	118	33
y	0b01101110	0x6E	110	34
Z	0b01011011	0x5B	91	35
blank	0b00000000	0x00	0	36
-	0b01000000	0x40	64	37
*	0b01100011	0x63	99	38
"""


import math
import RPi.GPIO as GPIO
import threading
from time import sleep, localtime


GPIO.setwarnings(False)
GPIO.setmode(GPIO.BCM)

HexDigits = [0x3F, 0x06, 0x5B, 0x4F, 0x66, 0x6D, 0x7D, 0x07, 0x7F, 
            0x6F, 0x77, 0x7C, 0x39, 0x5E, 0x79, 0x71, 0x3D, 0x76, 
            0x06, 0x1E, 0x76, 0x38, 0x55, 0x54, 0x3F, 0x73, 0x67, 
            0x50, 0x6D, 0x78, 0x3E, 0x1C, 0x2A, 0x76, 0x6E, 0x5B,
            0x00, 0x40, 0x63, 0xFF]

ADDR_AUTO = 0x40
ADDR_FIXED = 0x44
STARTADDR = 0xC0
# DEBUG = False


class TM1637:
    __doublePoint = False
    __Clkpin = 0
    __Datapin = 0
    __brightness = 1.0  # default to max brightness
    __currentData = [0, 0, 0, 0]

    def __init__(self, CLK, DIO, brightness):
        self.__Clkpin = CLK
        self.__Datapin = DIO
        self.__brightness = brightness
        GPIO.setwarnings(False)
        GPIO.setup(self.__Clkpin, GPIO.OUT)
        GPIO.setup(self.__Datapin, GPIO.OUT)

    def cleanup(self):
        """Stop updating clock, turn off display, and cleanup GPIO"""
        self.StopClock()
        self.Clear()
        GPIO.cleanup()

    def Clear(self):
        b = self.__brightness
        point = self.__doublePoint
        self.__brightness = 0
        self.__doublePoint = False
        data = [0x7F, 0x7F, 0x7F, 0x7F]
        self.Show(data)
        # Restore previous settings:
        self.__brightness = b
        self.__doublePoint = point

    def ShowInt(self, i):
        s = str(i)
        self.Clear()
        for i in range(0, len(s)):
            self.Show1(i, int(s[i]))

    def Show(self, data):
        for i in range(0, 4):
            self.__currentData[i] = data[i]

        self.start()
        self.writeByte(ADDR_AUTO)
        self.br()
        self.writeByte(STARTADDR)
        for i in range(0, 4):
            self.writeByte(self.coding(data[i]))
        self.br()
        self.writeByte(0x88 + int(self.__brightness))
        self.stop()

    def Show1(self, DigitNumber, data):
        """show one Digit (number 0...3)"""
        if(DigitNumber < 0 or DigitNumber > 3):
            return  # error

        self.__currentData[DigitNumber] = data

        self.start()
        self.writeByte(ADDR_FIXED)
        self.br()
        self.writeByte(STARTADDR | DigitNumber)
        self.writeByte(self.coding(data))
        self.br()
        self.writeByte(0x88 + int(self.__brightness))
        self.stop()
    
    # Scrolls any integer n (can be more than 4 digits) from right to left display.
    def ShowScroll(self, n):
        n_str = str(n)
        k = len(n_str)

        for i in range(0, k + 4):
            if (i < k):
                self.Show([int(n_str[i-3]) if i-3 >= 0 else None, int(n_str[i-2]) if i-2 >= 0 else None, int(n_str[i-1]) if i-1 >= 0 else None, int(n_str[i]) if i >= 0 else None])
            elif (i >= k):
                self.Show([int(n_str[i-3]) if (i-3 < k and i-3 >= 0) else None, int(n_str[i-2]) if (i-2 < k and i-2 >= 0) else None, int(n_str[i-1]) if (i-1 < k and i-1 >= 0) else None, None])
            sleep(1)

    def SetBrightness(self, percent):
        """Accepts percent brightness from 0 - 1"""
        max_brightness = 7.0
        brightness = math.ceil(max_brightness * percent)
        if (brightness < 0):
            brightness = 0
        if(self.__brightness != brightness):
            self.__brightness = brightness
            self.Show(self.__currentData)

    def ShowDoublepoint(self, on):
        """Show or hide double point divider"""
        if(self.__doublePoint != on):
            self.__doublePoint = on
            self.Show(self.__currentData)

    def writeByte(self, data):
        for i in range(0, 8):
            GPIO.output(self.__Clkpin, GPIO.LOW)
            if(data & 0x01):
                GPIO.output(self.__Datapin, GPIO.HIGH)
            else:
                GPIO.output(self.__Datapin, GPIO.LOW)
            data = data >> 1
            GPIO.output(self.__Clkpin, GPIO.HIGH)

        # wait for ACK
        GPIO.output(self.__Clkpin, GPIO.LOW)
        GPIO.output(self.__Datapin, GPIO.HIGH)
        GPIO.output(self.__Clkpin, GPIO.HIGH)
        GPIO.setup(self.__Datapin, GPIO.IN)

        while(GPIO.input(self.__Datapin)):
            sleep(0.001)
            if(GPIO.input(self.__Datapin)):
                GPIO.setup(self.__Datapin, GPIO.OUT)
                GPIO.output(self.__Datapin, GPIO.LOW)
                GPIO.setup(self.__Datapin, GPIO.IN)
        GPIO.setup(self.__Datapin, GPIO.OUT)

    def start(self):
        """send start signal to TM1637"""
        GPIO.output(self.__Clkpin, GPIO.HIGH)
        GPIO.output(self.__Datapin, GPIO.HIGH)
        GPIO.output(self.__Datapin, GPIO.LOW)
        GPIO.output(self.__Clkpin, GPIO.LOW)

    def stop(self):
        GPIO.output(self.__Clkpin, GPIO.LOW)
        GPIO.output(self.__Datapin, GPIO.LOW)
        GPIO.output(self.__Clkpin, GPIO.HIGH)
        GPIO.output(self.__Datapin, GPIO.HIGH)

    def br(self):
        """terse break"""
        self.stop()
        self.start()

    def coding(self, data):
        if(self.__doublePoint):
            pointData = 0x80
        else:
            pointData = 0

        if(data == 0x7F or data is None):
            data = 0
        else:
            data = HexDigits[data] + pointData
        return data
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
